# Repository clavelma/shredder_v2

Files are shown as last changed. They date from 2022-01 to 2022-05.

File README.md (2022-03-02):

 # Introduction
 
 #### 1. Motivation
   * The team has chosen to to work on recycling plastic waste during a school project. All the teams members are enthousiast by the idea.

 #### 2. Goal
   * Provide a thecnical and organisational solution tho recycle plastic waste. For this project the plastic essentially comes from 3D printing part.
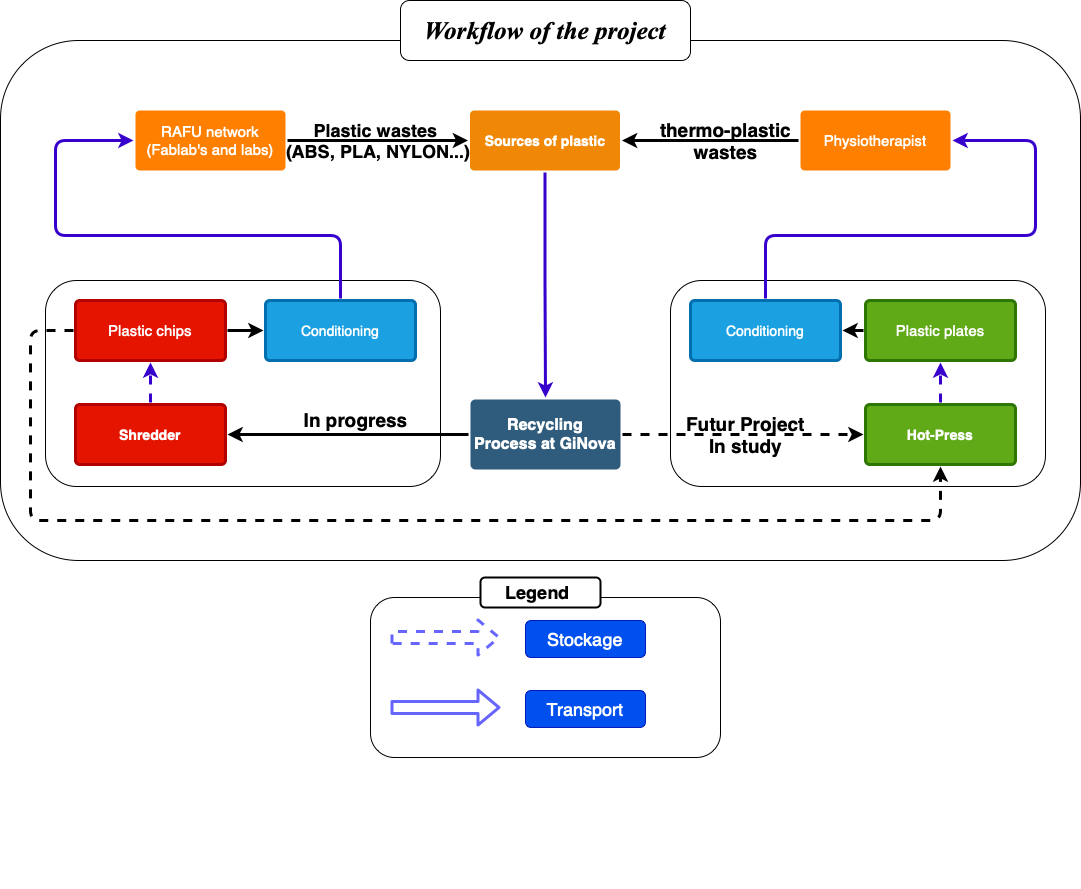
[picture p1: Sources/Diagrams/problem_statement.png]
Problem_statement


 #### 3. History
   * Initiators of the original project: Guillaume Marin
   * URL of other related project: [Precious plasitc](https://preciousplastic.com)
 #### 4. Documentation structure
   * Section 1: Introduction
   * Section 2: Specification
   * Section 3: Design
   * Section 4: Manufacturing
   * Section 5: Assembly
   * Section 6: Use
   * Section 7: Maintenance
   * Section 8: Disposal
 #### 5. Required skills
   * The project echopen need basic knowledge about electrical connection, ...
 #### 6. Contribution process
   * ...
 #### 7. Last update
   * 09/12/2021, 14h, addition of information, Margaux
 #### 8. Project team
   * BIANCIOTTO Tom {tom.bianciotto@grenoble-inp.org}
       * Role in the project: Project manager
       * https://www.linkedin.com/in/tom-bianciotto-b9ba4b1b8
   * CLAVEL Maxime {maxime.clavel@grenoble-inp.org}
       * Role in the project: Data manager
       * https://www.linkedin.com/in/maxime-clavel-36a43a218
   * GASTON Louis {louis.gaston@grenoble-inp.org}
   * LEGARDEUR William {william.legardeur@grenoble-inp.org}
   * LENNE Margaux {margaux.lenne@grenoble-inp.org}
       * Role in the project: Organisation, gantt chart manager
       * https://www.linkedin.com/in/margaux-lenne-27981b208/
   * WILLIE Nsongurua Innocent {nsongurua-innocent.willie@grenoble-inp.org}
       * https://www.linkedin.com/in/nsongurua-willie-3b72781b5
       * Role in the project: Organisation, Advancement manager
#### 9. Licence
   * GPLv3
#### 10. Sponsors and partners
   * Name: Grenoble INP Génie Industriel
      * URL: https://genie-industriel.grenoble-inp.fr/
      * Address: 46 avenue Félix Viallet F-38031 Grenoble cedex 01
   
   * Name: FabMSTIC
      * URL: https://fabmstic.imag.fr/
      * E-mail address: fabmstic@univ-grenoble-alpes.fr
      * Address: 740 rue de la Piscine, 38400 Saint-Martin-d’Hères

   * Name: La Casemate
      * URL: https://lacasemate.fr/
      * E-mail address: accueil@lacasemate.fr
      * Address: 2 place Saint-Laurent 38000 Grenoble

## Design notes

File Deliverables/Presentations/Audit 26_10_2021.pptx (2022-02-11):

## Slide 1

OPEN SOURCE PLASTIC

RECYCLING MACHINE

Mardi 26 Octobre

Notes: WILLIAM

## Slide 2

Table of contents

1 - Recap of the previous audit

2 - Updated Gantt

3 - The installation of the hopper

4 - Wiring diagram

5 - First version of safety rules and regulations

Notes: WILLIAM

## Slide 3

Recap of the previous audit

Germain LEMASSON, FabManager FabMSTIC ; He wants ABS & PLA big ships plastic thanks to our low cost shredder

Manuel FRANÇOIS, Physiotherapist, Orthotist ; He wants new plastic plate thanks to our ‘hoven’ and the unusable piece of plastic given by him

Gantt & risk analysis

Presentation of the client and his expectations

Presentation of the physiotherapist and his expectations

Organisation

Systems engineering of the shredder

CAD and first progress

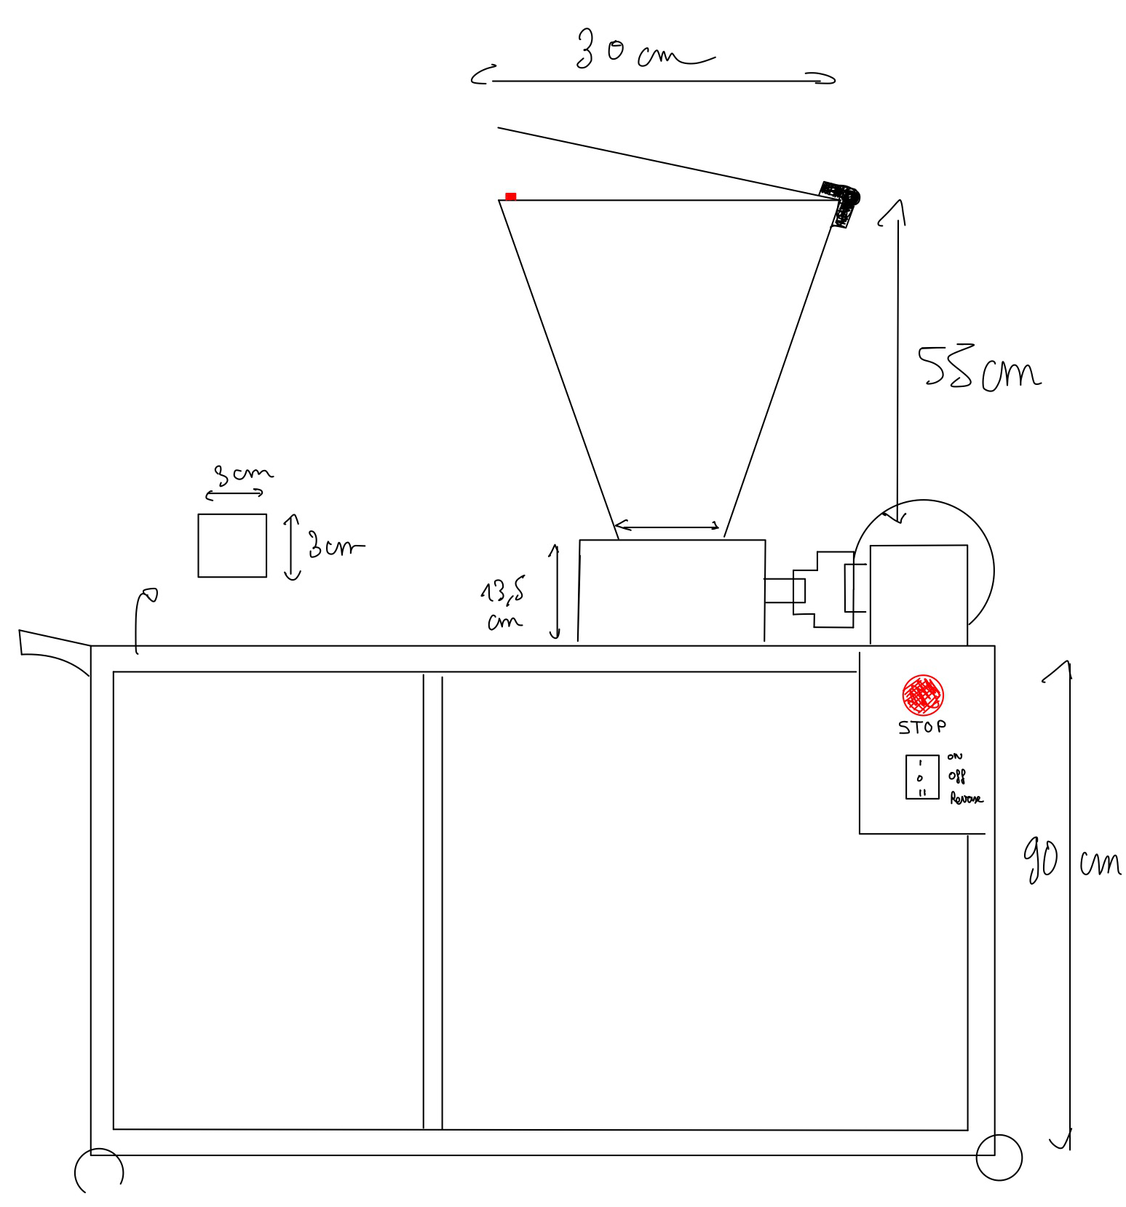
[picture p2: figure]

Stakeholders diagram

CAD of the hopper
Installation of the converter

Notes: MAXIME

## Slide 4

Table of contents

1 - Recap of the previous audit

2 - Updated Gantt

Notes: WILLIAM

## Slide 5

Updated Gantt

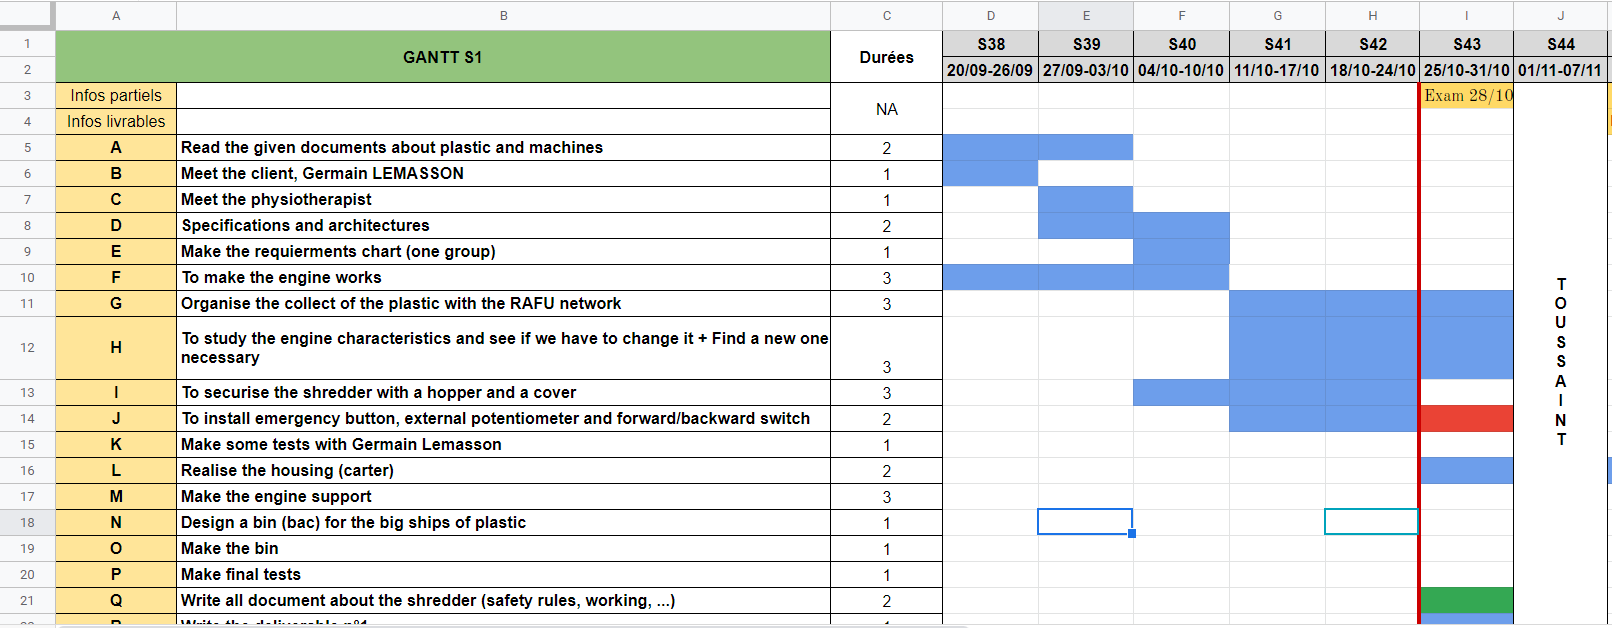
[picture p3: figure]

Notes: Someone else

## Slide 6

Table of contents

1 - Recap of the previous audit

2 - Updated Gantt

3 - The installation of the hopper

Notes: WILLIAM

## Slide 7

The installation of the hopper

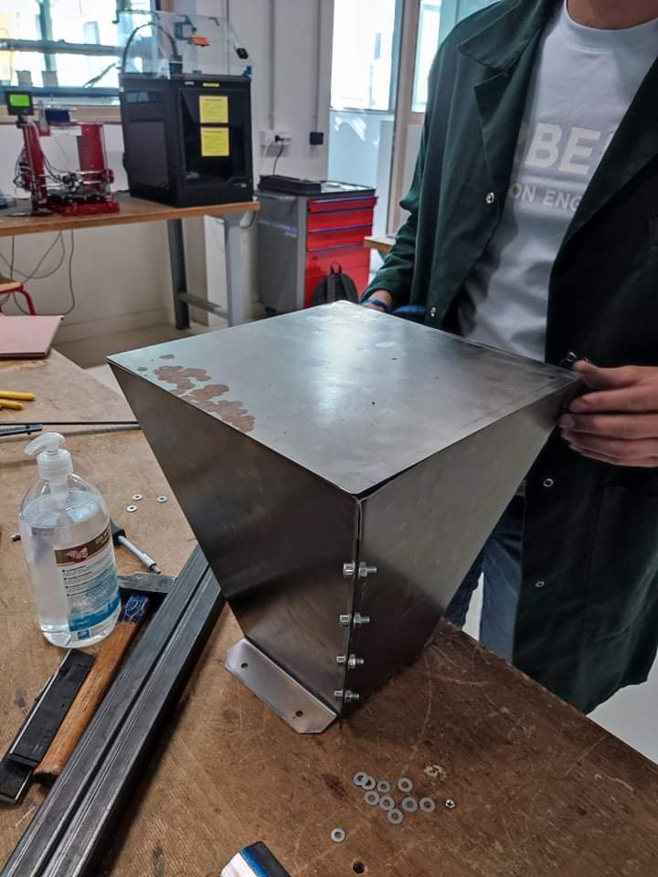
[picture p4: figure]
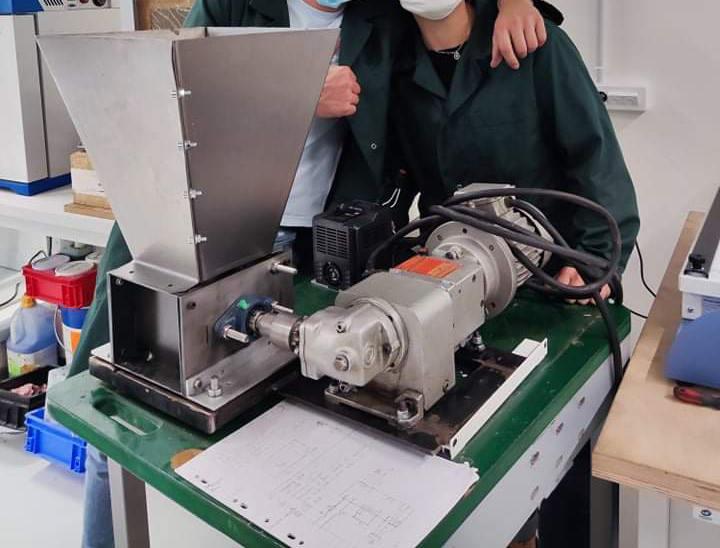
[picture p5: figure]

The final result

1. Bending of the 2 sheets
2. Assembly of the 2 parts
3. Attaching the hopper to the shredder

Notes: MAXIME

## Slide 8

Table of contents

1 - Recap of the previous audit

2 - Updated Gantt

3 - The installation of the hopper

4 - Wiring diagram

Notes: WILLIAM

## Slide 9

Wiring diagram

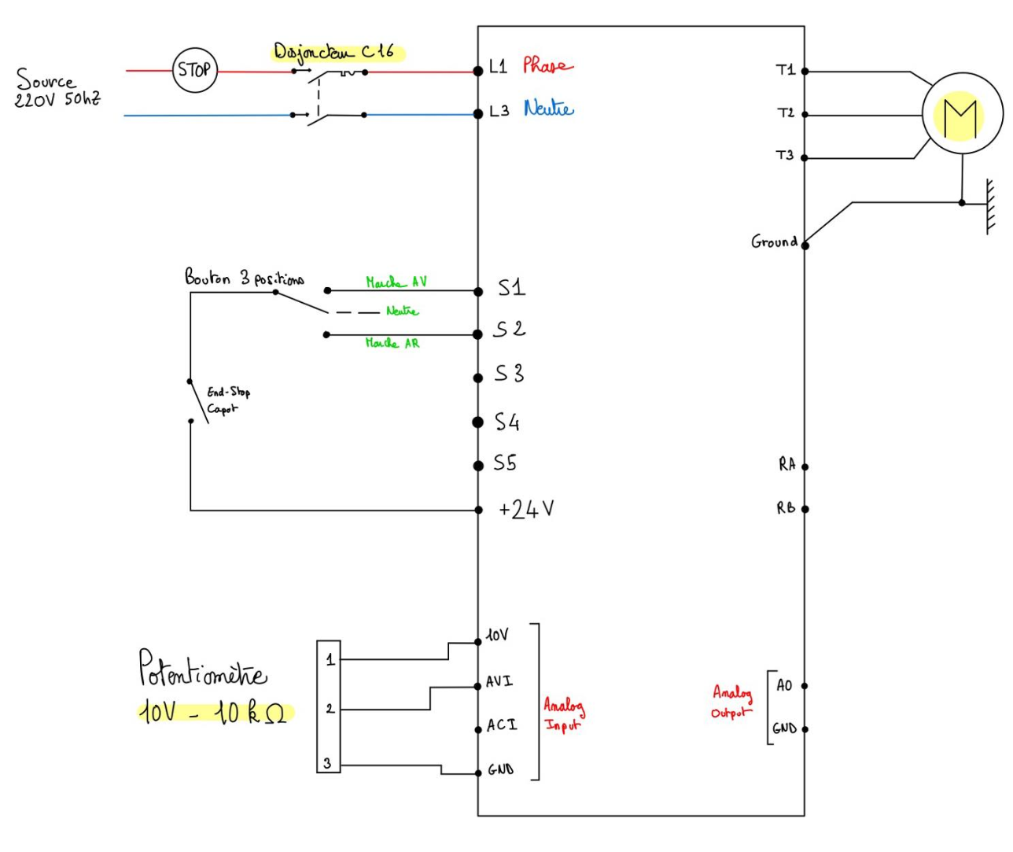
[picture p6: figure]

Buttons that will be present :
- Emergency stop with a circuit breaker (disjoncteur)
- Button on/off
- Button 3 positions
Other elements :
- End stop for the hopper
- A potentiometer
And the engine of course

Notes: Rajouter voyants pour allumer/éteint
Rajouter yellow flashing LED

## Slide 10

Table of contents

1 - Recap of the previous audit

2 - Updated Gantt

3 - The installation of the hopper

4 - Wiring diagram

5 - First version of safety rules and regulations

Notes: WILLIAM

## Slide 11

First version of safety rules and regulations

1. Avoid putting too much plastic into the shredder as this can wear down the motor.
2. When the machine is in motion, putting your hand into the crusher is forbidden to avoid injury.
3. Avoid putting hard objects to avoid damaging the blades.
4. Regularly lubricate and maintain the running parts.
5. Always clean the shredder after using it to shred a particular type of plastic.
6. Keep Jewelries, long hair, or loose clothing (i.e neckties) away from the plastic shredder opening.
7. Always turn off and unplug the power source when the machine is not in use.

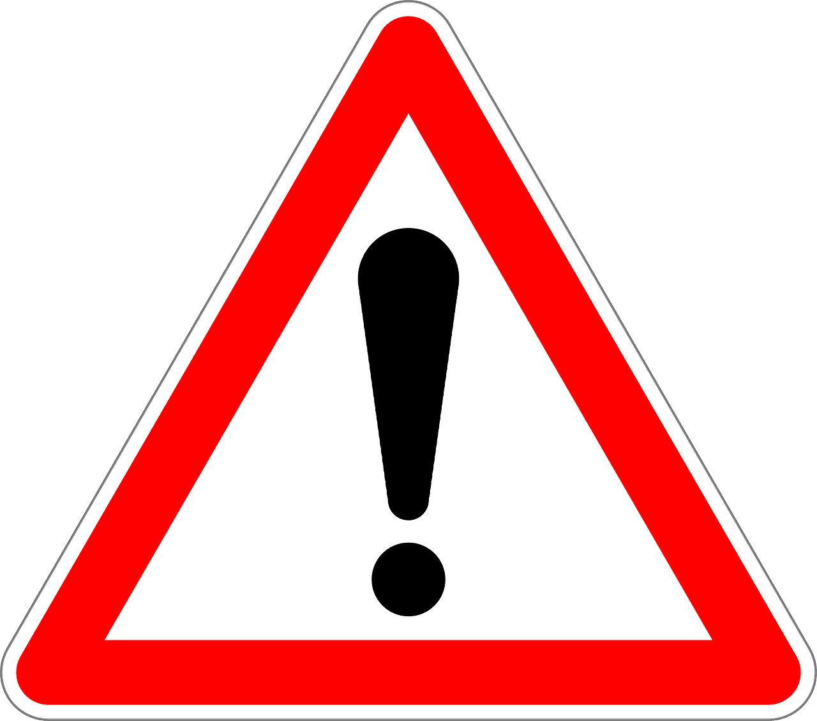
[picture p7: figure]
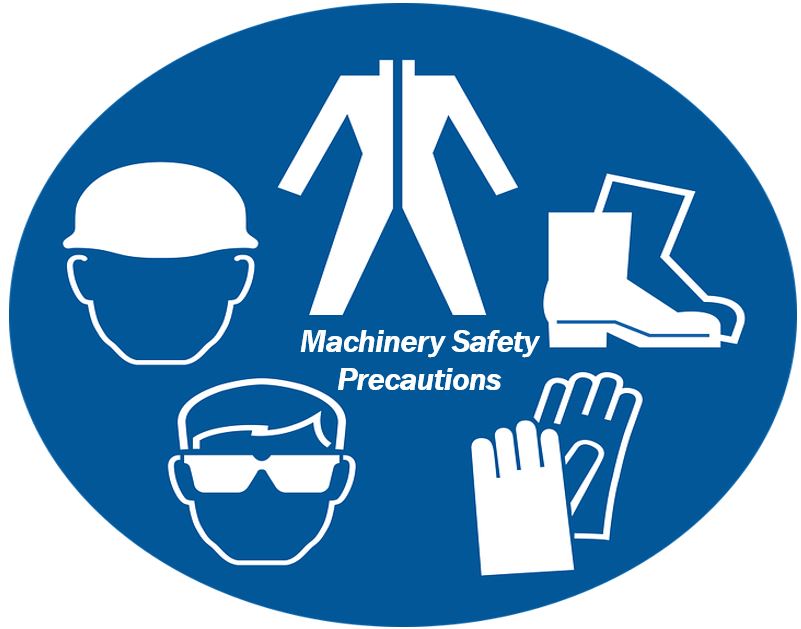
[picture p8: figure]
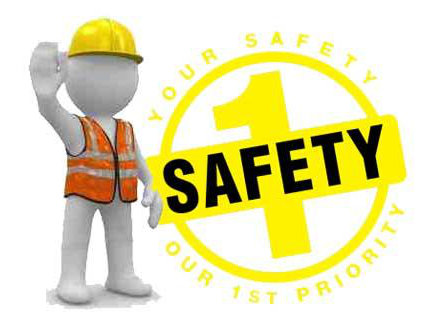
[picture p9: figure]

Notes: Someone else

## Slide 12

Interrogations

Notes: Someone else

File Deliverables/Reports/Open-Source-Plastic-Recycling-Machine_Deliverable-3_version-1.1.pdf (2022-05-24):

# Deliverable 3

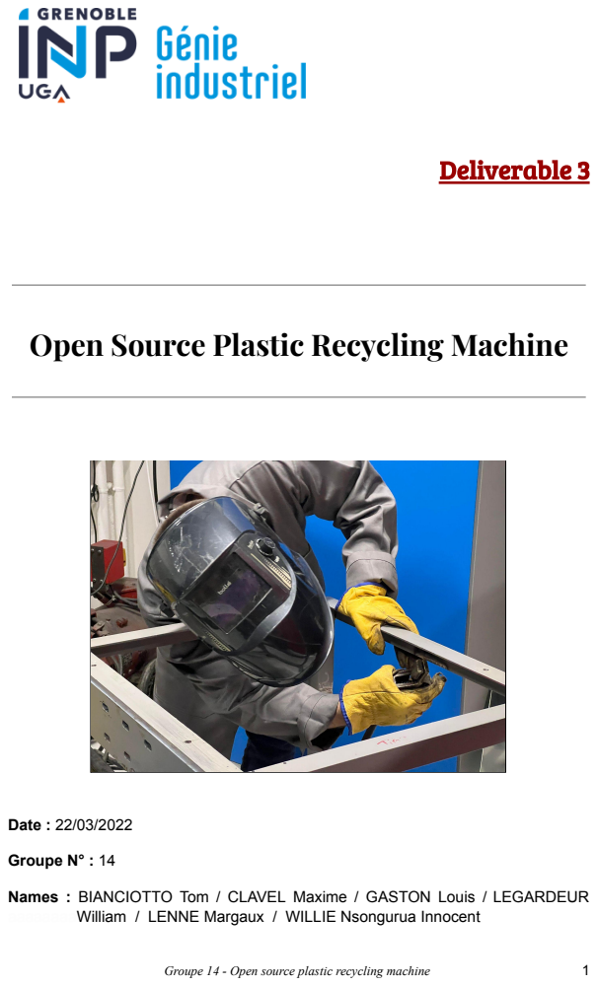
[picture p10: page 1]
Date : 22/03/2022; Groupe N° : 14; Names : BIANCIOTTO Tom / CLAVEL Maxime / GASTON Louis /; LEGARDEUR; Groupe 14 - Open source plastic recycling machine

Open Source Plastic Recycling Machine

aaaaaaaaWilliam / LENNE Margaux / WILLIE Nsongurua Innocent

# SUMMARY

A/ Context of the study - Main objective of the project | 3
B/ Architecture | 4
C/ Verify plan | 5
D/ Simulation (new) | 7
E/ Prototype | 9
F/ Project tasks advancement and achieved work plan | 12
G/ Risk analysis | 13
H/ Work Plan - objective, Key elements, difficulties | 14
APPENDIX 1: GANTT chart | 15
APPENDIX 2: Risk analysis | 17
APPENDIX 3: Cost table | 18
Groupe 14 - Open source plastic recycling machine | 2

## A/ Context of the study - Main objective of the project

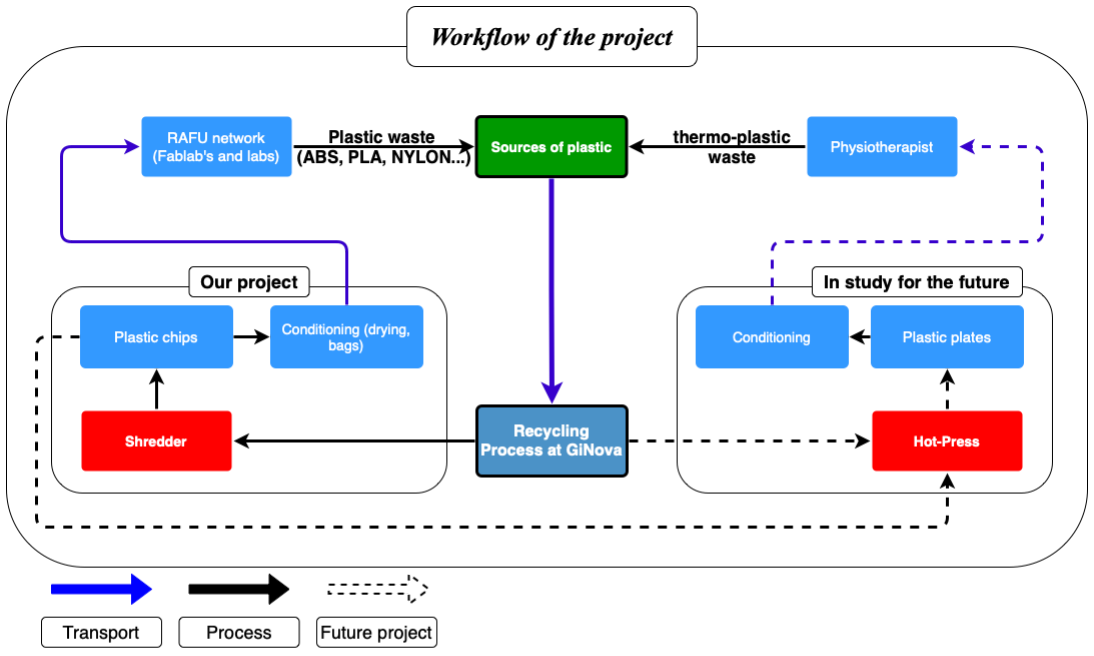
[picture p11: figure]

Figure 1 : Context of the project

The objective of our project can be summarized by finding an open source solution to recycle different kinds of plastic waste. In our more specific situation the objective is to first provide a plastic recycling solution to the RAFU network. This network gathers the labs and Fablab of the UGA. The research and the craft made there, create plastic waste especially with the 3D printing process. It would be a huge improvement if it became possible to recycle these plastics. In the future this solution could be extended to other kinds of actors who use plastics such as physiotherapists who make splints with thermoplastic or industrial materials (such as Chabloz company with nylon waste).

The objective of the group was to find a way to make the creation of 3D printing filament easier with the professional recycling machine available in the fabMSTIC. The main point of improvement is to work on the size of the pieces of plastic that had to be recycled. Another important phase is to organize the collection and the travel between the different recycling spots and users. Another point that could be developed is the creation of plastic plates to give a new life to the plastic collected.

To work on this project, the group was given a prototype of a plastic shredder and a hot-press. These two prototypes were not fully finished and need to be improved in a matter of capacity and mostly about safety to be used properly.

Since the first deliverable the work was focused between a fine study of the way to recycle plastic, the design of the prototypes improvement, and the creation of the Open source documentation on a Github repository. (https://github.com/clavelma/shredder_v2)

Groupe 14 - Open source plastic recycling machine | 3

## B/ Architecture

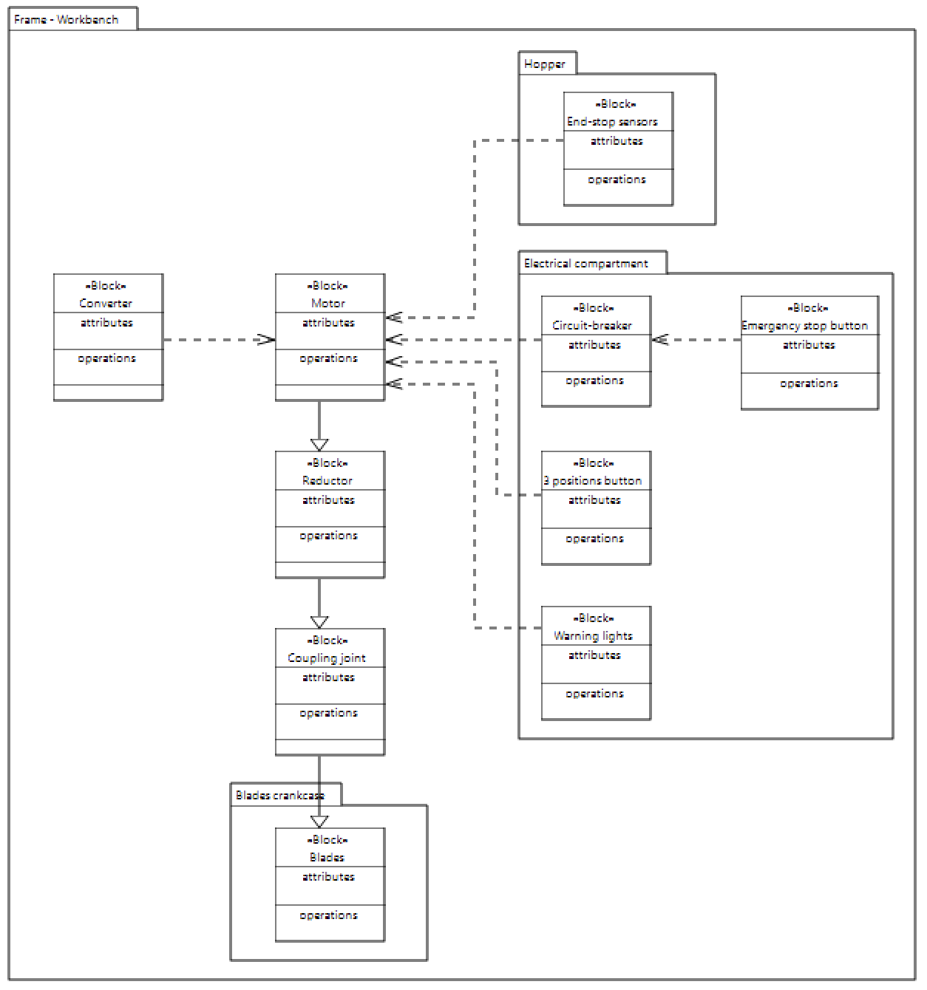
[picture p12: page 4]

To have a better view of the products of our project, we made an Internal block diagram for both the shredder and the compactor. It allows to represent the connections between components but also, and especially, the exchanges of matter, energy and information with the notion of ports.

Groupe 14 - Open source plastic recycling machine | 4

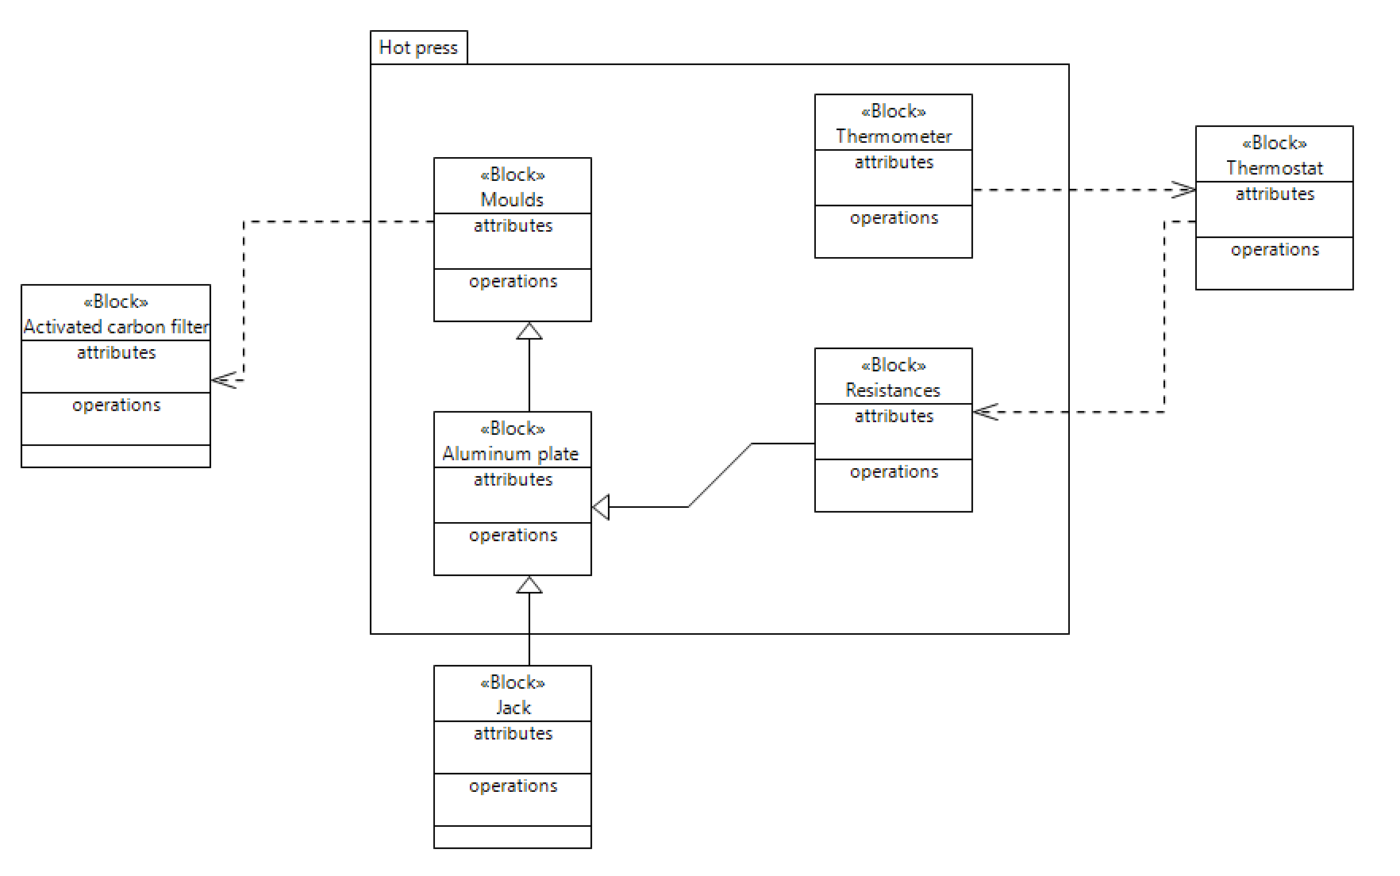
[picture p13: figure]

Figure 2 : Internal block diagram Shredder & Compactor

Informations/ Electrical energy

Forces/ Mechanical energy

Groupe 14 - Open source plastic recycling machine | 5

## C/ Verify plan

In order to follow the requirements requested by the customer, we list them in a table [figure 3] and for each of them we assign one of three levels:

- Not verified: meaning that we have not yet been able to verify this requirement. However, verification plans exist and will be implemented as soon as possible.
- In progress: meaning that we are currently working on the mill to validate this requirement.
- Verified: everything has already been implemented to validate the requirement.
ID requirement | Name | Level of verification
FR1 | The shredder needs to work on a standard 220V 50Hz EU plug. | Verified: use of a converter
FR2 | The shredder needs to respect the 1m50x1mx1m50 maximum volume to avoid cluttering the space. | Verified
FR3 | The shredder needs to shred plastic into chips with a surface inferior to 15 mm² with a tolerance of 5%. | Not verified: requires a test phase when the shredder will be operational
FR4 | The shredder needs to stop in case of emergency in less than 3 seconds. | Not verified: requires a test phase when the shredder will be operational
FR5 | The shredder must be secured to prevent injury on contact (against moving parts and projectiles). | In progress: a hopper and a cover have been installed. Lack a protective cover for rotating parts and the installation of an end-stop button to switch off the engine if the cover is opened
FR6 | The shredder needs to have a power-on and/or operation indication that the operator can see | In progress: provided on the electrical diagram but not connected yet
FR7 | The shredder must not exceed the maximum accepted noise level. | Not verified: requires a test phase when the shredder will be operational
FR8 | The shredder should not transform one of the labs and fablabs of the RAFU network into a storage place for all the plastic chips. | Verified: use of kanban labels to track each bag of chips
FR9 | The shredder needs to have a reverse function in case of blocking or any other mechanical problem. | Verified: thanks to the converter
FR10 | The shredder and its installation should be stable and strong. | Verified: through structural calculations

Figure 3 : Monitoring of the requirements

So we have three requirements that are not yet verified at the time of writing this deliverable. Let us detail the verification plans for these:

- FR3 "The shredder needs to shred plastic into chips with a surface inferior to 15 mm² with a tolerance of 5%." :
Groupe 14 - Open source plastic recycling machine | 6

For the test phase, we will cut different types of grids with different holes in steel using the water jet cutter [see figure 4] (plexiglass is impossible to use because it is brittle and the grate is right under the teeth of the rotating grinder. This grid will be placed under the shredder, just below its blades. Thus, if the chips are too large, they are recovered by the blades and returned to be crushed until they reach the size desired by the customer.

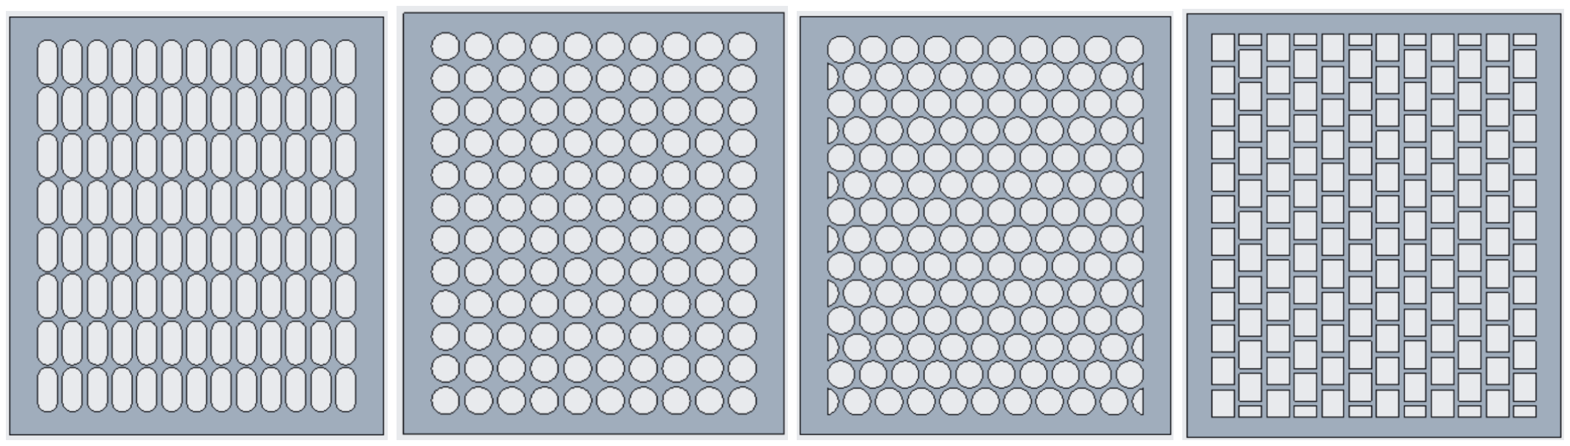
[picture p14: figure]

Figure 4 : Different kind of grid to test

- FR4 "The shredder needs to stop in case of emergency in less than 3 seconds". :

In order to verify this requirement, we plan to use the blocked week to have two people from the group work on the converter ramp study. Indeed, by choosing the right parameters on the one we already have we will be able to configure the new ordered converter correctly once we receive it.

- FR7 "The shredder must not exceed the maximum accepted noise level. :

This requirement will be verified once the prototype is completed. Potential noise sources are mainly from :
→ From the engine
→ From the shredding of the plastic, but the first shredding test we did with the old engine showed us that the noise emitted was still acceptable.
→ From the workbench
Groupe 14 - Open source plastic recycling machine | 7

## D/ Simulation (new)

In the previous deliverables, we were talking about reinforcing the support structure of our workbench, supporting the shredder assembly and the motor, actually made of a 30 mm MDF wooden plate. This idea was quite rushed and our professors asked us to prove the necessity of changing this plate, so now we do :

The system we have, transmits high torque by the upper plate of the table, the reason why is that the motor and the shredder are two independant parts so they must necessarily be attached to a common support : the wooden plate. We would not want it to break under the effect of the engine torque so we decided to make a small simulation of the situation, described on [figure 5] below :

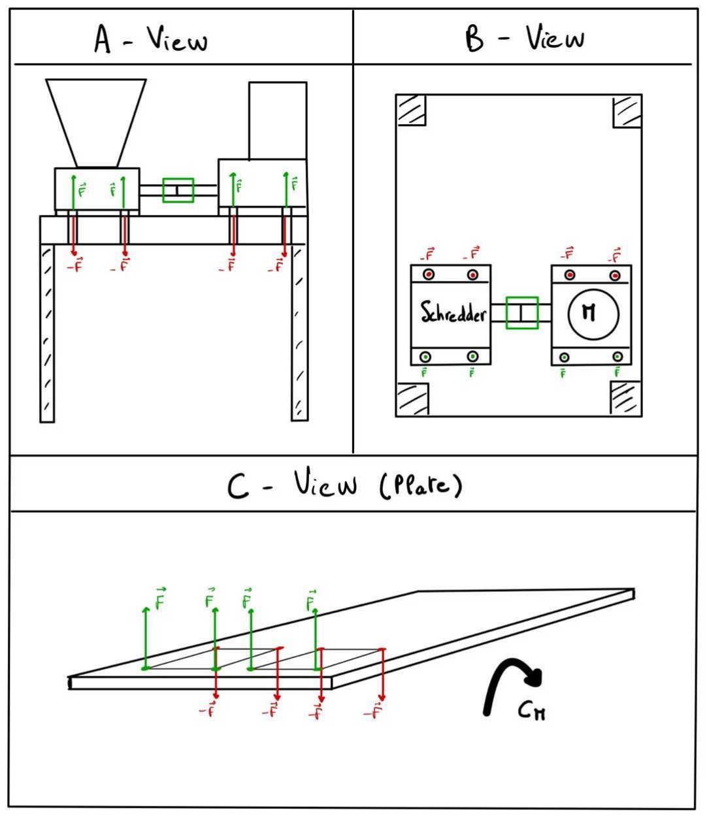
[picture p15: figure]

Figure 5 : Representation of the efforts due to engine torque

Groupe 14 - Open source plastic recycling machine | 8

Now we have a simple but realistic schematic of what will really happen on the plate. We can get further into it by modeling this schematic on a structural calculation software, here we will use ANSYS Workbench.

By assumption, we are considering that the torque is equally distributed in the 8 fixation points, we also make the hypothesis that the radius of the blades is about 8 cm. If we take a torque of 300 N.m (maximum transmitted torque), we obtain (300/0,08)/8 = 470 N on each hole of fixation.

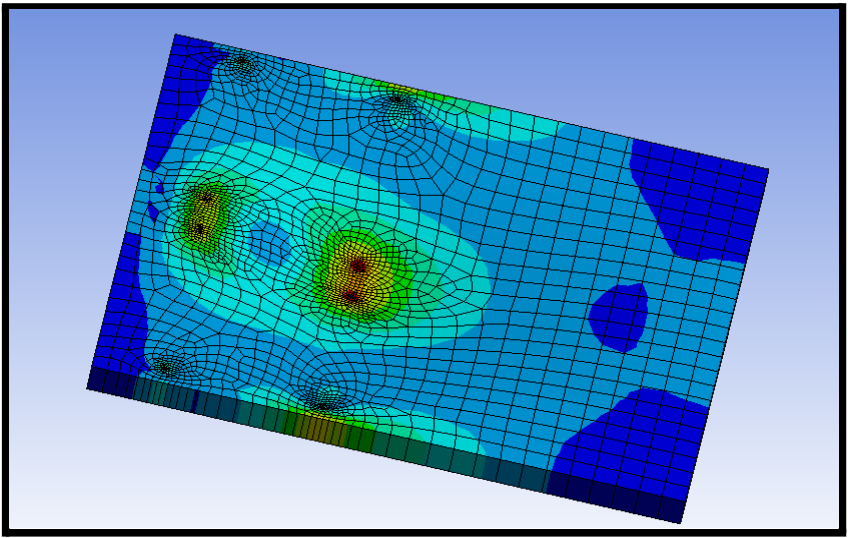
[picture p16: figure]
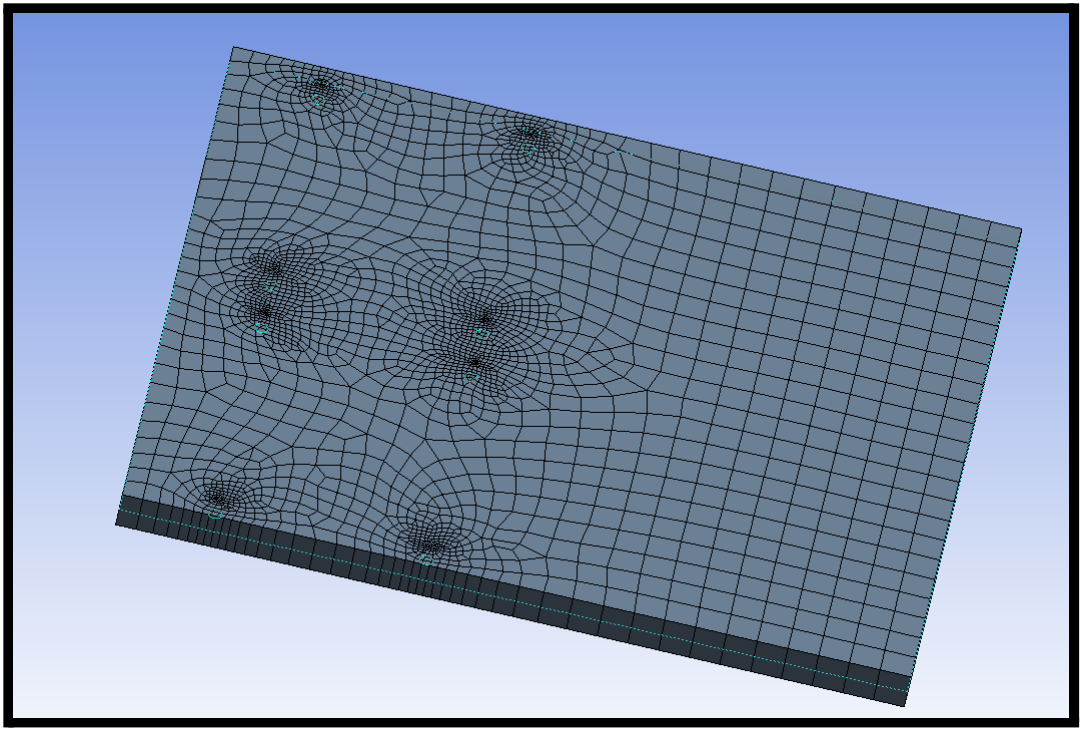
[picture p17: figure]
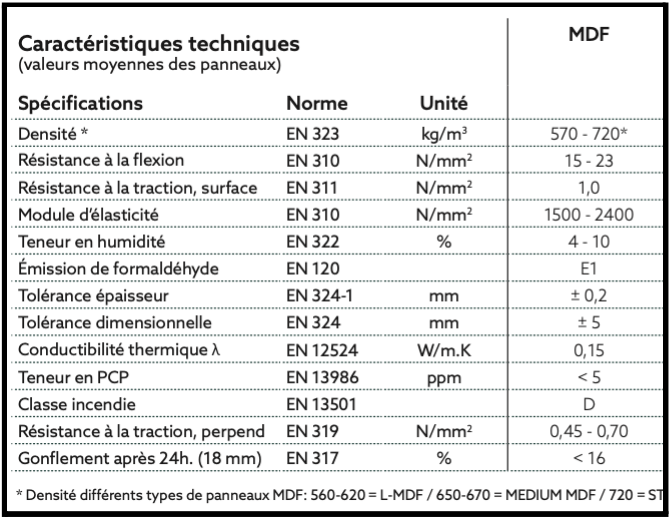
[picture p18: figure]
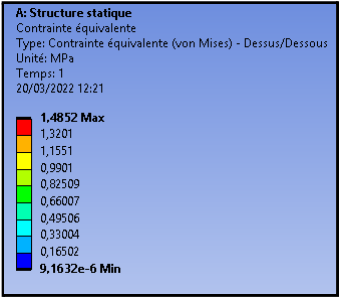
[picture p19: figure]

Figure 6 : Resistance of MDF wood [decopan.com]

As we can see, the maximum constraint is about 1.5 Mpa on the wooden plate, regarding [Figure 6], MDF can absorb around 20 Mpa of bending so the plate seems solid enough to support all these efforts.

Groupe 14 - Open source plastic recycling machine | 9

## E/ Prototype

While waiting for our new adapted gear motor we tried to make as much progress as possible on the structure of our shredder, two important things were missing:

- A chip collection tray
- An electrical compartment

To put these elements in place, it was necessary to add a floor to our frame, so we prepared the structure and welded square steel profiles of 30x30 mm.

We then fixed a wooden plate for the shelf and a plexiglass plate as a front for the different switches: emergency stop, forward/backward/off switch, potentiometer, circuit breaker. A separating sheet has also been installed to prevent people from electrical injuries putting their hands in the electrical part. For safety reasons, all the metal elements will be connected to the ground.

We obtain the following structure (still incomplete) [Figure 7]:

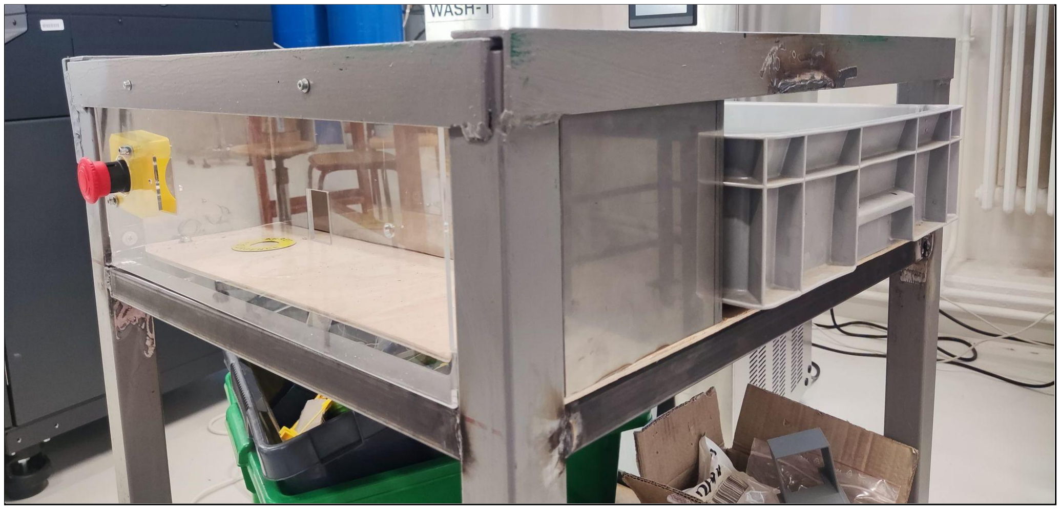
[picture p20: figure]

Figure 7 : Structure of the shredder

Groupe 14 - Open source plastic recycling machine | 10

We also installed our hinges and the opening sensor on the hopper [Figure 8]:

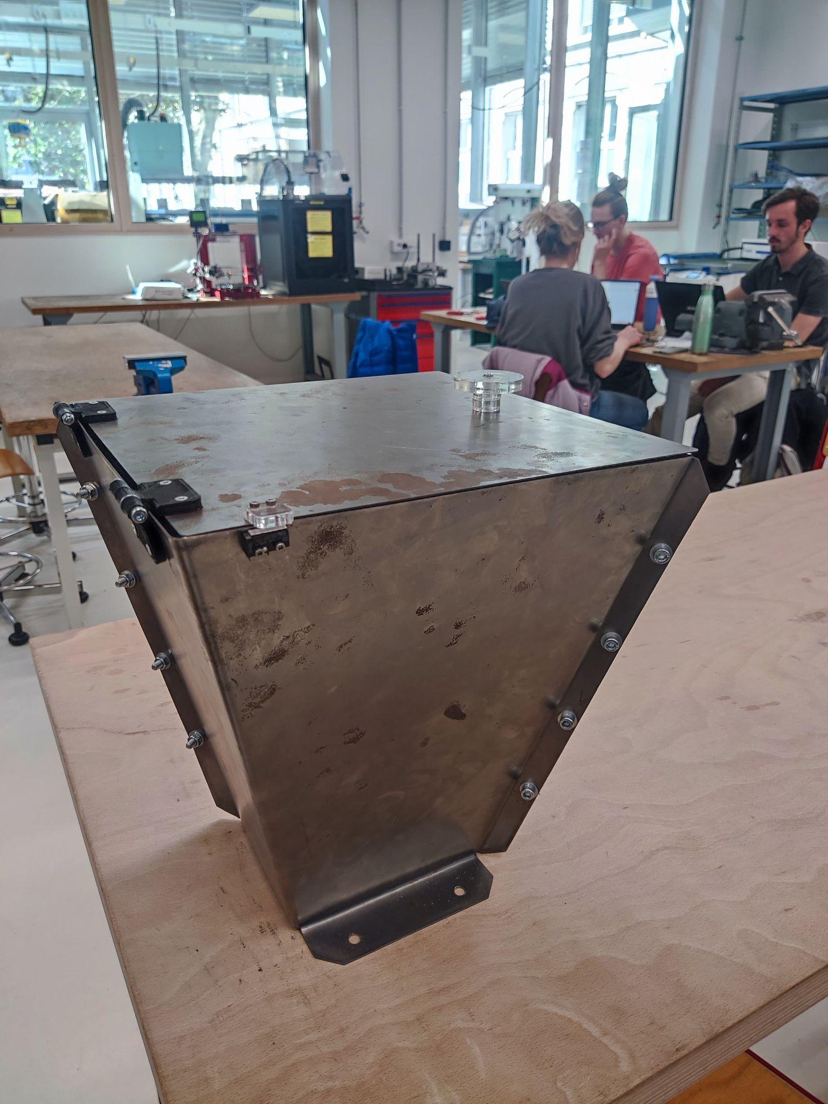
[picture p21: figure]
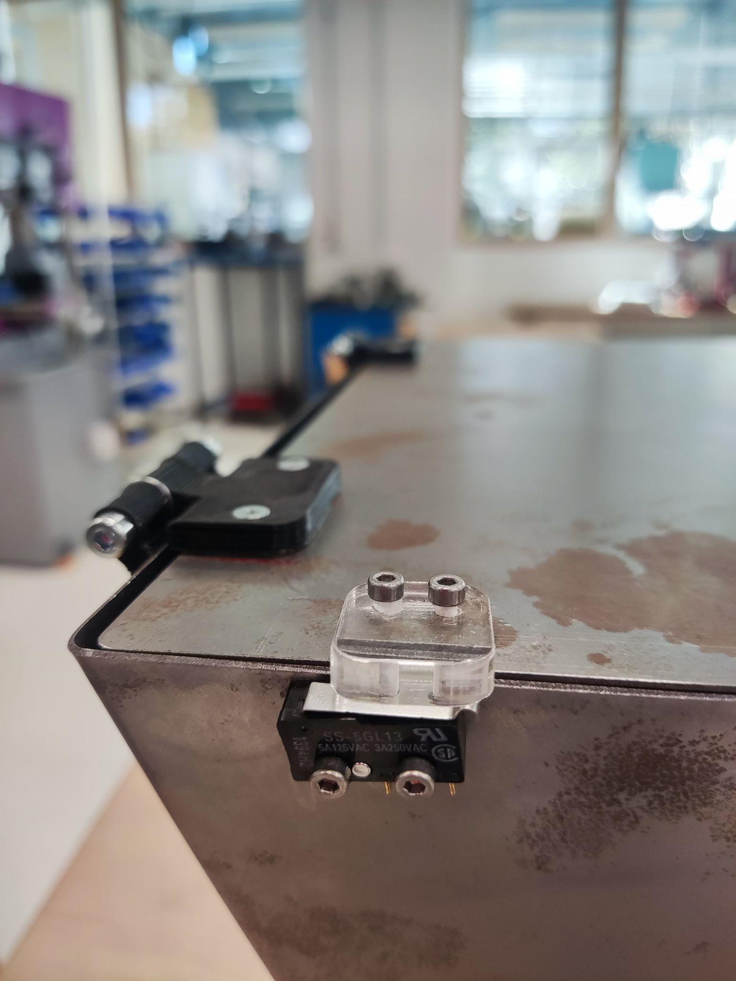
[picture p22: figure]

Figure 8 : Hinges, handle and opening sensor on the hopper of the shredder

We now have to make the various attachments for the transmission according to the specifications of the new gear motor ordered, cut a steel sheet for the shelf (currently made of a poor wooden plate) and an aluminum sheet for an enhanced rigidity of the front panel (currently made of plexiglas).

As explained above (Part C/ Verify plan), we also need to cut out different backflow grids for the chips to determine their optimal size. We therefore go to ENSE3 to make all our cut-outs [Figure 9] :

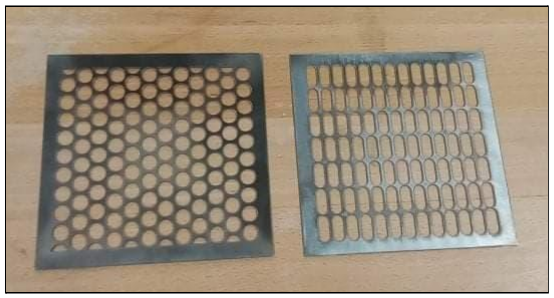
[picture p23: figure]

Figure 9 : Backflow grids for the shredder

Now, the next step for these grids will be to create a sheet metal forming die to form the sheet into a cylinder.

Groupe 14 - Open source plastic recycling machine | 11

## F/ Project tasks advancement and achieved work plan

Since the last audit, the tasks have gone according to the Gantt chart. We only had a one week delay on task D "Systems Engineering" because we had not finished the SysML part of the hot press on papyrus. However, this delay does not have a big impact on our project as it is not on the critical path.

For the next few weeks, we have to pay close attention to task I "Improvement of the shredder" which is a critical path task. Indeed, as planned, this task must be finished by week 15 (11 April - 17 April) in order to make room for the last task of the critical path: "Tests" [see annex 1]. However, if we look at the subtasks of I, we notice that many of them are on stand-by [see figure 10]. The reason for this is that the motor given by Guillaume MARIN (the engineer who gave us a first prototype of the shredder at the beginning of the year) had insufficient torque, as did the second motor we found in Ginova. This necessitated a calculation phase in order to find the torque we needed for shredding plastic. We are now waiting for this new motor and a new converter, as the old one is not suitable for the future motor. [See G/ Risk analysis for more details].

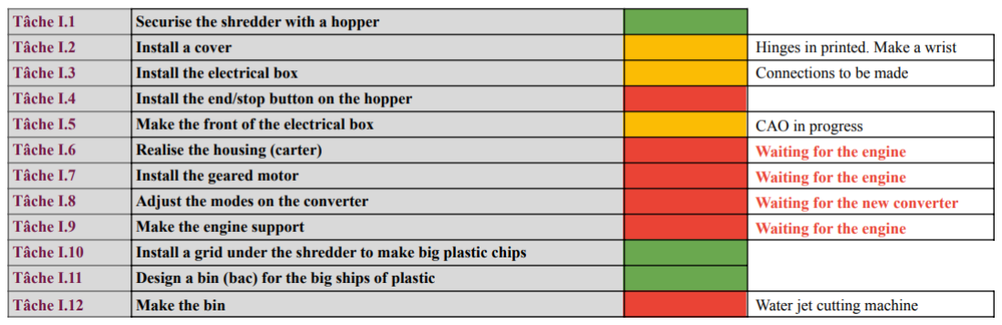
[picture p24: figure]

Figure 10 : Details of task I - Improvement of the shredder
(red = task not started, orange = task in progress, green = task finished)

While waiting for this new engine, we will take advantage of the week blocked for the project activities to make as much progress as possible on the prototype of the shredder. When we receive the motor, all we have to do is install it and connect it to the shredder shaft.

We also made an update of the project cost estimations [appendix 3] where we mainly add the engineering price and the new gearmotor quote with its new converter.

Groupe 14 - Open source plastic recycling machine | 12

## G/ Risk analysis

At the period of the last deliverable, the group got some issue with the engine which was not powerful enough for the shredding task. This possibility was considered in the Risk analysis but the criticality was clearly under-estimated. To not make the same error the group had decided to reconsider all the severity and occurrence levels of the previous Risk Analysis document to create a new revision of the document. This revision number 2 is focused on two main points. First reconsider all the critical levels as said before with the experience we had gained during the first phases of the project in order to highlight all the major risks for the end of the project. The second part of the work in the Risk Analysis is to think about the new issues that could occur in the prototyping and testing phase.

For the new evaluation of the risk levels, we can take the example of the risk of an engine that is too weak to shred that passed from a Criticality 1 to 4 that is clearly more reasonable after experiencing this problem. Some other risks were re-evaluated : to finish the prototyping, we need to receive a new engine with enough torque, a problem in the order could compromise the end of the project. We can also talk about the fact that the lab might be occupied by other students, that could prevent us from working on the prototype. At this period this risk is more important because first year students have some project that needs the lab. The access to the tools and equipment could be pretty difficult during these phases.

Figure 11 : Motor risk in REV1

Figure 12 : Motor risk in REV2

About the New risks that were added they are mainly related to the prototyping and testing phase. A very obvious risk in this kind of phase could be to break a component while mounting it or while testing it. To find a solution to this problem or to try to limit at maximum the chance of this happening, the group had made a list of all the components of the prototype. In this list the group will define what components are the more fragile or the most difficult to replace. This could help to be more careful when we manipulate the more critical parts of the prototype. Another risk could be about the shredding module which could possibly not work as expected. We never saw it work because of the engine issue and we completely do not know how it will shred the plastic parts.

Figure 13 : Risks added in REV2

Groupe 14 - Open source plastic recycling machine | 13

## H/ Work Plan - objective, Key elements, difficulties

As compared to the first few months when we started, we can boldly say that we have a clear work plan and end goal now. In the first few months of our project, we were solely focused on the global perspective of our project, instead of being specific on a particular area (functional shredder). We had indeed underestimated the demand of the work. Thanks to several educating sessions with the professors, we are more focused on the specifics and now have a clear goal.

The objective of our work, in correlation to the topic, is to deliver a functional plastic shredding machine, with detailed documentation on GitHub, as it is an open source project. With this objective in mind, our shredder should be able to shred plastics to the desired fineness, for other usage. The key elements of this machine are the motor, blades, torque and the electrical components of the shredder. To determine the performance of our shredder, different tests will be carried out on the shredding machine. For example, the ratio of the output mass to the input mass will be determined and a high percentage indicates a good shredding process.

So far, we have had a fair share of difficulties in the course of this project, especially as stated above concerning the global and specific objective of our project. We had underestimated the demands of the project and tried to fulfill the global objective in such a short time, which is clearly impossible. Another major difficulty has been with the motor of the shredder. It had a lower capacity and therefore could not power the machine. We finally made a new order but now there is a delay. Also we did not follow completely accurate procedures, this could have been the cause. In the first two deliverables, we did not include SysML diagrams and we had ignored a lot of engineering aspects in our presentations, especially to aid in communicating effectively our project. All these have been rectified. We are gradually but clearly working on delivering a finished prototype.

As regards the documentation on GitHub, as a team, we have made commendable progress. We have clearly defined the task for everyone, and had to redefine roles, so as to get everyone involved in the project and deliver on time. The report takes this format, a weekly update of tasks carried out by each member of the team and their progress, this is done by the project advancement manager. The gantt manager updates the gantt regularly, each member also has a part to update on the platform. The project manager oversees.

Therefore, at the end of the project, we should be able to deliver a functioning shredder, able to shred plastics to the desired fineness, thanks to the grid. And also make it an open source project, thanks to GitHub.

Groupe 14 - Open source plastic recycling machine | 14

# APPENDIX 1: GANTT chart

Link to go to the drive with the gantt chart (to see the sub-tasks): https://docs.google.com/spreadsheets/d/1zl9KApmCFzgjy7fXfSUUbfGAa_7RfqJYZSNwacTICsc/edit?usp=sharing (https://docs.google.com/spreadsheets/d/1zl9KApmCFzgjy7fXfSUUbfGAa_7RfqJYZSNwacTICsc/edit?usp=sharing)

You can also see directly a sample below :

Groupe 14 - Open source plastic recycling machine | 15

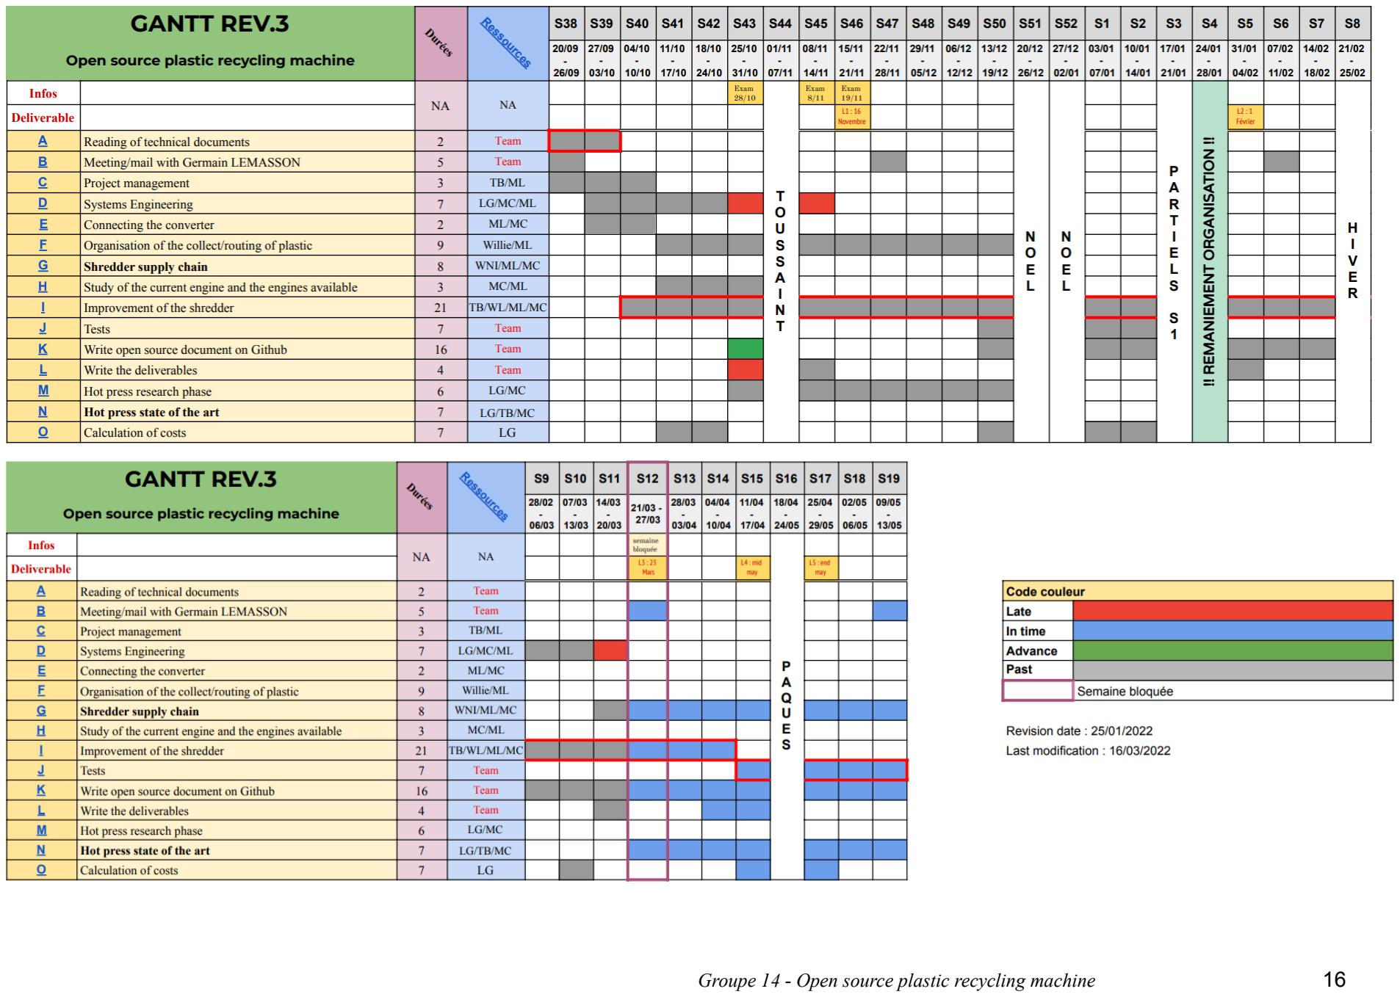
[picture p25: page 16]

Groupe 14 - Open source plastic recycling machine | 16

# APPENDIX 2: Risk analysis


Groupe 14 - Open source plastic recycling machine | 17

# APPENDIX 3: Cost table


Groupe 14 - Open source plastic recycling machine | 18

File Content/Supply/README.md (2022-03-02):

# **Supply**

*Dans notre projet, nous parlerons de supply afin d'assurer le contrôle des différents plastiques passant dans le broyeur. Nous avons alors chercher un moyen de connaître l'origine, le type et la quantité de plastique broyé, l'identité de la personne utilisant le broyeur, ainsi que les différentes opérations subies par le plastique. Afin d'assurer cette traçabilité, nous avons alors pensé à nous inspirer de la méthode kanban que nous avons vu en 1ere année d'école d'ingénieur.   *

## **Storage**

Dans notre logistique, lorsque du plastique sera broyé avec le broyeur, les copeaux tomberont dans un grand bac en plastique. Ensuite les copeaux passeront dans le séchoir (étape non obligatoire mais recommandée surtout si les copeaux sont destinés à recréer du filament pour les imprimantes 3D). Finalement, ils seront placé dans un 

## **Kanban label**

kanban_label

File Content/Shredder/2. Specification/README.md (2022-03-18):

# **Specification**

*The specification consists in describing the product with a "black box" external view to capture the intermediate technical objects (stakeholders, external interfaces, services, and constraints) that serve to, *in fine*, elucidate the product requirements.*

## **How to document the specifications?** 
  
## **1. Stakeholders:**

stakeholders_shredder drawio

## **2. External interfaces**

*The image below shows the external interfaces of  ADD-ONS of XYZ cargo as a graph*

Image of External interfaces of XYZ cargo-ADD ONS

<a href="https://app.diagrams.net/?libs=general#Hamerezoji1362%2Fdrawio-github%2Fmaster%2FExternal%20interfaces.drawio">Edit As New</a> | <a href="https://app.diagrams.net/#Hamerezoji1362%2Fdrawio-github%2Fmaster%2FExternal%20interfaces.png">Edit in diagrams.net</a>
</details>

### Template of external interfaces
   
   * Clients
       * needs
   * Users
       * use
       * repair
   * Partners
       * data
       * technical support
   * Media
       * reproduce
       * data
   * European standards
       * laws
       * norms
       * security
   * Environment
       * supply
       * adapt
       * reuse
       * technical support
  
 Image of stakeholder diagram for template
  
   *The link below can be used to define the external interfaces of your project/product.*
  
  <a href="https://app.diagrams.net/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">Edit As New</a> | <a href="https://app.diagrams.net/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">Edit in diagrams.net</a>

## 3. Service *(synonyms: external function, capability)* 
<details>
  <summary>Click to see the guideline!</summary>
  
- **Definition:** *A service is an effect intended by a stakeholder resulting from the interaction of the product with its environment (i.e. what the  product is for).*

- **Comments:**
  - *Services provide users with an exchange value that can be included in an economic system (e.g. airlines buy flight hours).*
  - *Services are intended effects that can be observed from outside the product ("black box" external view), but not from outside an internal component ("white box" internal view).*
  - *Services are defined in a solution neutral-way.*
  - *Services can be stated as follows: The [Product] shall enable [Stakeholder] [Action verb] (e.g. The product shall enable end-user to clean its teeth)*
  - *we often reason in terms of action verbs to communicate expected behaviors, so it would be nice to be able to search designs with action verbs*
</details>

<details>
  <summary>Click to see the example!</summary>
  
 ```
  What does contain the minimum documentation of the service to stakeholders?
  
  Example of services for ADD-ONS of XYZ Cargo
  
    - The ADD-ONS shall enable the food producer to store food
      - 1.1 solid (10 kilos)
      - 1.2 liquid (5 litrs)
    - The ADD-ONS shall enable the food producer to heat food
      -  2.1solid (150 deg Celcius)
      - 2.2 liquid (80 deg Celcius)
    - The ADD-ONS shall enable the food producer to cool down food for 4 hours
      - 3.1 solid (6 deg Celcius)
      - 3.2 liquid (6 deg Celcius)
      
    - ...
  ```
 </details>

### Template of services
  
   * Services to clients
       * The shredder shall enable the ABS&PLA plastic from 3D printing scraps to be reduce into medium or small chips.
       * The shredder shall enable the thermoformable plastic from thermoformable plastic plate scraps to be reduce into medium or small chips.
   * Services to users
       * The shredder shall enable the plastic from user's personal collection to be reduce into medium or small chips.
   * Services to partners
       * The shredder shall enable the plastic from partner's personal collect to be reduce into medium or small chips.
   * Services to media
       * The shredder will serve as a functional example of low tech solution for plastic recycling.
   * Services to european standards
       * The shredder will meet the safety and working standard conditions based on european standards. 
   * Services to environment
       * The shredder in all ramifications, will be safe to use and environmental friendly.

## 4. Constraint *(Synonyms: non function requirement)*

### Template of constraints
  
   * The shredder should be dismantled for recycling purposes
   * The shredder should be realise and operate in a low tech philosophy
   * The shredder should follow the european standards
   * Open source community should be able to reproduce it
   * User should be able to use it in security
   * Ginova should be able to handle the maintenance
   * The shredder should be incorporating in Ginova
   * The shredder should be able to shred the plastic from the collect
   * The shredder should be built using the maximum of the existing prototype
   * The shredder assembly and user should be accessible and open source
   * The shredder should be realised thanks to the RAFU network facility
   * The shredder should be able to go forward and to go backward

## **5. Requirement**
 
 ### Template of requirements
    
   * FR1:  The shredder needs to work on a standard 220V 50Hz EU plug
   * FR2:  The shredder needs to respect the 1m50x1mx1m50 maximum volume
   * FR3:  The shredder needs to shred plastic into chips with a surface inferior to 1cm²
   * FR4:  The shredder needs to stop in case of emergency in less than 3 seconds
   * FR5:  The shredder must be secured to prevent injury on contact (against moving parts and projectiles)
   * FR6:  The shredder needs to have a power-on and/or operation indication that the operator can see
   * FR7:  The shredder must not exceed the maximum accepted noise level
   * FR8:  The shredder should not transform one of the labs and fablabs of the RAFU network into a storage place for all the plastic chips.
   * FR9:  The shredder needs to have a reverse function in case of blocking or any other mechanical problem
   * FR10: The shredder and its installation should be stable and strong.

(The effects of vibration can be severe. Unchecked vibration can accelerate rates of wear (e.g., reduce bearing life) and damage equipment. Vibrating machinery can create noise, cause safety problems and lead to degradation in plant working conditions.)

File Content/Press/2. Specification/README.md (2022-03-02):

# **Specification**

*The specification consists in describing the product with a "black box" external view to capture the intermediate technical objects (stakeholders, external interfaces, services, and constraints) that serve to, *in fine*, elucidate the product requirements.*

## **How to document the specifications?** 
  
## **1. Stakeholders:**

stakeholders_shredder drawio

## **2. External interfaces**

*The image below shows the external interfaces of  ADD-ONS of XYZ cargo as a graph*

Image of External interfaces of XYZ cargo-ADD ONS

<a href="https://app.diagrams.net/?libs=general#Hamerezoji1362%2Fdrawio-github%2Fmaster%2FExternal%20interfaces.drawio">Edit As New</a> | <a href="https://app.diagrams.net/#Hamerezoji1362%2Fdrawio-github%2Fmaster%2FExternal%20interfaces.png">Edit in diagrams.net</a>
</details>

### Template of external interfaces
   
   * Clients
       * needs
   * Users
       * use
       * repaire
   * Partners
       * data
       * technical support
   * Media
       * reproduce
       * data
   * European standards
       * laws
       * norms
       * security
   * Environment
       * supply
       * adapt
       * reuse
       * technical support
  
 Image of stakeholder diagram for template
  
   *The link below can be used to define the external interfaces of your project/product.*
  
  <a href="https://app.diagrams.net/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">Edit As New</a> | <a href="https://app.diagrams.net/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">Edit in diagrams.net</a>

## 3. Service *(synonyms: external function, capability)* 
<details>
  <summary>Click to see the guideline!</summary>
  
- **Definition:** *A service is an effect intended by a stakeholder resulting from the interaction of the product with its environment (i.e. what the  product is for).*

- **Comments:**
  - *Services provide users with an exchange value that can be included in an economic system (e.g. airlines buy flight hours).*
  - *Services are intended effects that can be observed from outside the product ("black box" external view), but not from outside an internal component ("white box" internal view).*
  - *Services are defined in a solution neutral-way.*
  - *Services can be stated as follows: The [Product] shall enable [Stakeholder] [Action verb] (e.g. The product shall enable end-user to clean its teeth)*
  - *we often reason in terms of action verbs to communicate expected behaviors, so it would be nice to be able to search designs with action verbs*
</details>

<details>
  <summary>Click to see the example!</summary>
  
 ```
  What does contain the minimum documentation of the service to stakeholders?
  
  Example of services for ADD-ONS of XYZ Cargo
  
    - The ADD-ONS shall enable the food producer to store food
      - 1.1 solid (10 kilos)
      - 1.2 liquid (5 litrs)
    - The ADD-ONS shall enable the food producer to heat food
      -  2.1solid (150 deg Celcius)
      - 2.2 liquid (80 deg Celcius)
    - The ADD-ONS shall enable the food producer to cool down food for 4 hours
      - 3.1 solid (6 deg Celcius)
      - 3.2 liquid (6 deg Celcius)
      
    - ...
  ```
 </details>

### Template of services
  
   * Services to clients
       * The shredder shall enable the ABS&PLA plastic from 3D printing scraps to be reduce into big or medium chips
       * The shredder shall enable the thermoformable plastic from thermoformable plastic plate scraps to be reduce into big or medium chips
   * Services to users
       * The shredder shall enable the plastic from user's personal collect to be reduce into big or medium chips
   * Services to partners
       *  The shredder shall enable the plastic from partner's personal collect to be reduce into big or medium chips
   * Services to media
       * x
   * Services to european standards
       * x 
   * Services to environment
       * x 

## 4. Constraint *(Synonyms: non function requirement)*

### Template of constraints
  
   * The shredder should be dismantled for recycling purposes
   * The shredder should be realise and operate in a low tech philosophy
   * The shredder should follow the european standards
   * Open source community should be able to reproduce it
   * User should be able to use it in security
   * Ginova should be able to handle the maintenance
   * The shredder should be incorporating in Ginova
   * The shredder should be able to shred the plastic from the collect
   * The shredder should be built using the maximum of the existing prototype
   * The shredder assembly and user should be accessible and open source
   * The shredder should be realised thanks to the RAFU network facility
   * The shredder should be able to go forward and to go backward

## **5. Requirement**
 
### Template of requirements
    
   * FR1: The compactor needs to work on a standard 220V 50Hz EU plug
   * FR2: The compactor needs to be able to melt PLA (175°C)
   * FR3: The compactor needs to compact plastic plates with a thickness of 1.6, 2.5 and 3.2 mm
   * FR4: The compactor needs to filter the toxic air
   * FR5: The compactor needs to be isolated
   * FR6: The compactor needs to be safe for the operator (heat)
   * FR7: The compactor needs to have a power-on and/or operation indication that the operator can see
   * FR8: The compactor should have a thermometer (to set the temperature)

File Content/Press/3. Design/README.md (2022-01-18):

# Design

*"To design" refers to the process of originating and developing a plan for a product. So, the product models provide consideration of concepts of product design. Product models serve to answer questions that interest multiple views on the product. Among the product views, there is an agreed-upon ontology of product models named Function-Behaviour-Structure (FBS) where:*

- **Function (F)** stands for **“what the object is for”.**
- **Behaviour (B)** stands for **“what the object does”.**
- **Structure (S)** stands for **“what the object consists of”.**

Image of FBS of design

> *Figure 1. Same function, different behaviour, different structure (Rosenman & Gero, 1998)* 

*Moreover, it should describe the complexity of the product via:* 
- **Modular architecture** that describes **“architecture of functions and instructions of the product”.**

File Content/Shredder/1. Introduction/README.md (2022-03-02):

# Introduction

*The introduction to the documentation aims to provide more details about the project goal, and context. This introduction should allow the reader to first understand the motivation of the project and also who is involved or has been involved in its creation. As this documentation structure aims at fostering the reuse of the technical contents of the project, it is important to understand well the context.*

<details>
  <summary>Click to see the guideline and examples!</summary>
  
## Motivations

*This section addresses the question: Why are you starting this project?*

As an example:
  
The project [BCN3D Moveo](https://github.com/BCN3D/BCN3D-Moveo/) is motivated by the high cost 
of the materials that undergraduate students must use for learning how to engineer mechatronics systems.

## Goals

*This section addresses the question: What will be delivered in this project?* 

As an example: 
  
The project [BCN3D Moveo](https://github.com/BCN3D/BCN3D-Moveo/) is an open source robotic arm 
that everyone should be able to replicate - with or without modification - at home without the need for highly 
technical knowledge and expensive materials. 
The robotic arm will support several of the existing training itineraries: 
mechanical design, automation, industrial programming, etc.

## History

*Here it is of neccessity to acknowledge the existing sources that have been used in this project with locations*

- Initiators of the original project
- URL of the original project
- URL of other related projects 

## Documentation structure

*How is your documentation organized?*

These guidelines will provide you with a standard structure that is mainly following the product 
life cycle and the technological decomposition. It is implemented in the documentation template available in this project. 
  
For example:
- Introduction
- Specification
- Design 
- Manufacturing
- Assembly
- Use
- Maintenance
- Disposal

And inside each of the sections, if required:
- Mechanical
- Electronic 
- Software 

## Required skills

*What is the specific knowledge a maker should own to reuse - with or without modification - your product??*

For example:
  
The project echopen need basic knowledge about the medical ultrasound technology such as ultrasound imaging, 
a matter of acoustical impedance, etc.  

## Contribution Process

*Describe here how a maker can contribute to your project*

-  Example of a contribution process:
  - Post an [issue] and briefly outline the changes you plan to make
  - If you are looking for input on what to contribute, browse the issues with the Requests or Bug label
  - Describe branches
  - Describe what a Pull Request (PR) shall contain (detailed description of changes, a summary of the test, 
    issue numbers that the PR resolves)
  - Specify code style 
  - Contributor license agreement

## Last updates 

*What is the last update of your documentation?*

- Last modification (date, time, object of modification, who,...)

## Project team

*Describe here who is the leader and the main contributors of the project*

- Name {E-mail}
  - domain of expertise and role in the project
  - link to personal web page

## License

*What open-source hardware license your project complies with?*

- [Comparison of free and open-source software licences](https://en.wikipedia.org/wiki/Comparison_of_free_and_open-source_software_licences)
- [license of open hardware projects](https://opensource.com/law/15/2/intro-open-hardware-licensing#:~:text=Open%20source%20hardware%20is%20hardware,on%20their%20hardware%20at%20all.)

## Sponsors and Partners

Who is sponsoring your project?

- URL:
- Name:
- E-mail address:

  </details>
  
### Template of introduction

 #### 1. Motivation
   * The team has chosen to work on recycling plastic waste during a school project. All the teams members are enthusiastic about the idea.

 #### 2. Goal
   * Provide a technical and organisational solution to recycle plastic waste. For this project the plastic essentially comes from 3D printing part.

 #### 3. History
   * Initiators of the original project: Guillaume Marin
   * URL of other related project: [Precious plasitc](https://preciousplastic.com)
 #### 4. Documentation structure
   * Section 1: Introduction
   * Section 2: Specification
   * Section 3: Design
   * Section 4: Manufacturing
   * Section 5: Assembly
   * Section 6: Use
   * Section 7: Maintenance
   * Section 8: Disposal
 #### 5. Required skills
   * The project plastic recycling machine needs basic knowledge about electrical connection, ...
 #### 6. Contribution process
   * ...
 #### 7. Last update
   * 01/3/2022, 14h, Edited, Nsongurua
 #### 8. Project team
   * BIANCIOTTO Tom {tom.bianciotto@grenoble-inp.org}
       * Role in the project: Project manager
       * https://www.linkedin.com/in/tom-bianciotto-b9ba4b1b8
   * CLAVEL Maxime {maxime.clavel@grenoble-inp.org}
       * Role in the project: Electronic and Systems Engineering manager 
       * https://www.linkedin.com/in/maxime-clavel-36a43a218
   * GASTON Louis {louis.gaston@grenoble-inp.org}
       * Role in the project: Data manager
   * LEGARDEUR William {william.legardeur@grenoble-inp.org}
   * LENNE Margaux {margaux.lenne@grenoble-inp.org}
       * Role in the project: Organisation, gantt chart manager
       * https://www.linkedin.com/in/margaux-lenne-27981b208/
   * WILLIE Nsongurua Innocent {nsongurua-innocent.willie@grenoble-inp.org}
       * Role in the project: Progress manager
       * https://www.linkedin.com/in/nsongurua-willie-3b72781b5
#### 9. Licence
   * GPLv3
#### 10. Sponsors and partners
   * Name: Grenoble INP Génie Industriel
      * URL: https://genie-industriel.grenoble-inp.fr/
      * Address: 46 avenue Félix Viallet F-38031 Grenoble cedex 01
   
   * Name: FabMSTIC
      * URL: https://fabmstic.imag.fr/
      * E-mail address: fabmstic@univ-grenoble-alpes.fr
      * Address: 740 rue de la Piscine, 38400 Saint-Martin-d’Hères

   * Name: La Casemate
      * URL: https://lacasemate.fr/
      * E-mail address: accueil@lacasemate.fr
      * Address: 2 place Saint-Laurent 38000 Grenoble

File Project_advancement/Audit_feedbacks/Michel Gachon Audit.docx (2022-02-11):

Requirement = what we propose to the client

make a table cross the line that are good

Important to do the revisions of documents (especially for Risk analysis that evolve a lot)

Manage the discussion with the customer to check regularly his needs.

anticipate meeting with customer

huge impact 3

sure 3

multiply the 2 figures

juste analyse 6,9,4 risk the other can be let down

→ faire évoluer au fil du temps

toujours 2 personnes responsables par livrable pour mettre à jour les documents (analyse des risques, gantt, requirements…)

identify the critical path

be careful with the examheiiiin

do the schedule for the whole year with less details, we can do more detailed schedules for semester for example.

Keep the annex on date for each deliverable to show how the evolution of the project

do the criteria analysis and logical structure.

Put the type of final deliverable (prototype + all the documentation) in the L1

__________________________________________

Audit

refaire toute l’analyse des besoin

faire une architecture logique

faire une IS complète sur la presse et se diviser le travail proprement

make studies

Faire un vrai gantt sur un logiciel spécialisé

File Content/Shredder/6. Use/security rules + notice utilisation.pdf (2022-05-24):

# Utilisation du broyeur de plastique

RISQUES ENCOURUS - E.P.I

RISQUE
D'ENTRAÎNEMENT
MÉCANIQUE

RISQUE DE
COUPURE DE LA
MAIN

PRÉCAUTIONS DE SÉCURITÉ !!!

- Lorsque la machine est en mouvement, il est interdit de mettre les mains dans le broyeur pour éviter iatoute blessure.
- Éviter de mettre trop de plastique d’un coup dans le broyeur car cela peut user le moteur.
- Nettoyez toujours le broyeur après l'avoir utilisé pour broyer un type différent de plastique.
- Dans la benne de récupération, ne pas mélanger différents types de plastique.
- Éloigner les bijoux, les cheveux longs ou les vêtements amples (par exemple, les cravates) de l'ouverture iadu broyeur.
- Ne jamais laisser fonctionner la machine sans surveillance.
- Garder les mains éloignées de toutes pièces en mouvement.
- En cas de dysfonctionnement, actionner le bouton d’arrêt d’urgence.

En cas d’incident, contacter immédiatement le personnel de GINOVA. N’hésitez pas à demander conseil auprès de ces personnes.

# Utilisation du broyeur de plastique

UTILISATION; 1/ Passer le disjoncteur sur ON; 2/ Mettre le bouton 3 positions sur :; aaiiOFF.

PROPRETÉ DU POSTE

En cas d’incident, contacter immédiatement le personnel de GINOVA. N’hésitez pas à demander conseil auprès de ces personnes.

- I (marche avant) pour mettre en route le broyeur
- II (marche arrière) en cas de problème comme dents bloquées

3/ Régler la vitesse de broyage grâce au potentiomètre

4/ Une fois le broyage terminé, mettre le bouton 3 positions sur 0 et remettre le disjoncteur sur

- Assurez-vous avant de partir de laisser le poste de travail dans un état de propreté convenable.
- Si vous changez de plastique à broyer, veillez à ce qu’il ne reste aucun copeaux d’autres type de iaplastique dans le broyeur.

POTENTIAL RISKS

### Utilisation of the shredder

MECHANICAL
RISK

HAND CUTTING
RISK

SECURITY PRECAUTIONS
❖ | When the machine is in motion, putting your hand into the crusher is forbidden to avoid injury.
❖ | Avoid putting too much plastic into the shredder as this can wear down the motor.
❖ | Always clean the shredder after using it to shred a particular type of plastic.
❖ | In the recycling bin, do not mix different types of plastic.
❖ | Keep jewelries, long hair, or loose clothing (i.e., neckties) away from the plastic shredder opening.
❖ | Never leave the machine running unattended.
❖ | Keep hands away from all moving parts.
❖ | Avoid putting hard objects to avoid damaging the blades.
❖ | Regularly lubricate and maintain the running parts.

In the event of an incident, contact GINOVA personnel immediately. Do not hesitate to seek advice from these people.

### Utilisation of the shredder

UTILISATION; 1/ Switch the circuit breaker to ON; 2/ Set the 3-position button to : - ON (forward) to start the grinder.; jammed teeth.; OFF.

CLEANLINESS OF THE STATION

- OFF (reverse) in case of problems such as

In the event of an incident, contact GINOVA personnel immediately. Do not hesitate to seek advice from these people.

3/ Adjust the grinding speed using the potentiometer.

4/ Once the grinding is finished, put the 3-position button on 0 and put the circuit breaker back on

- Make sure before leaving to leave the workstation in a suitable state of cleanliness.
- If you change the plastic to be shredded, make sure that there are no shavings of other types of plastic left in the shredder.

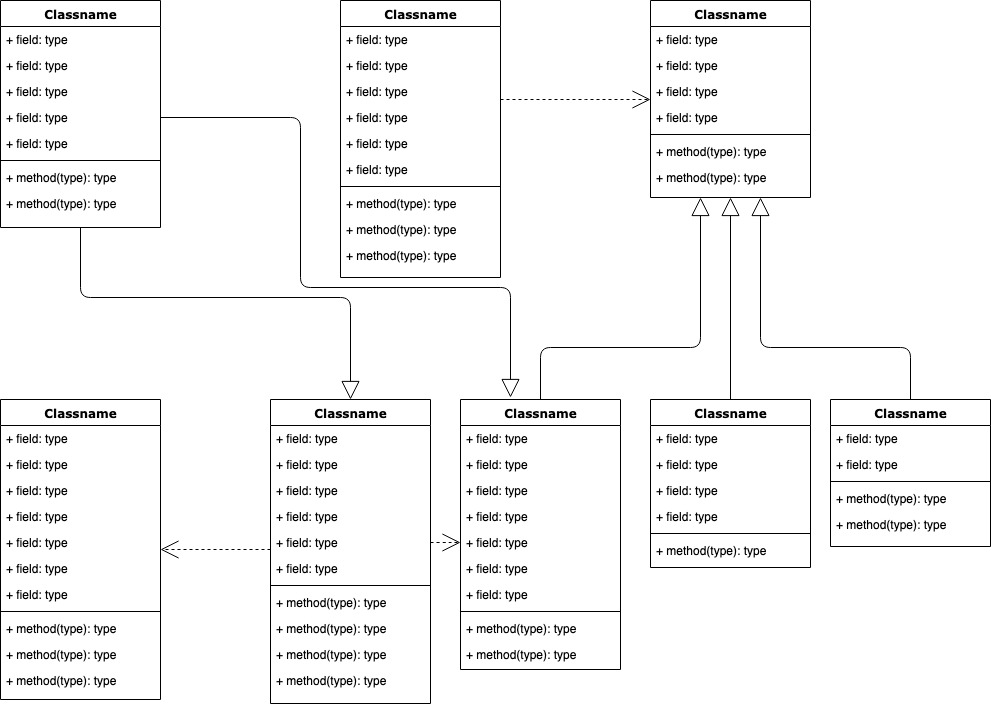
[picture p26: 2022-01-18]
Sources/Images/Template of software architecture.jpg

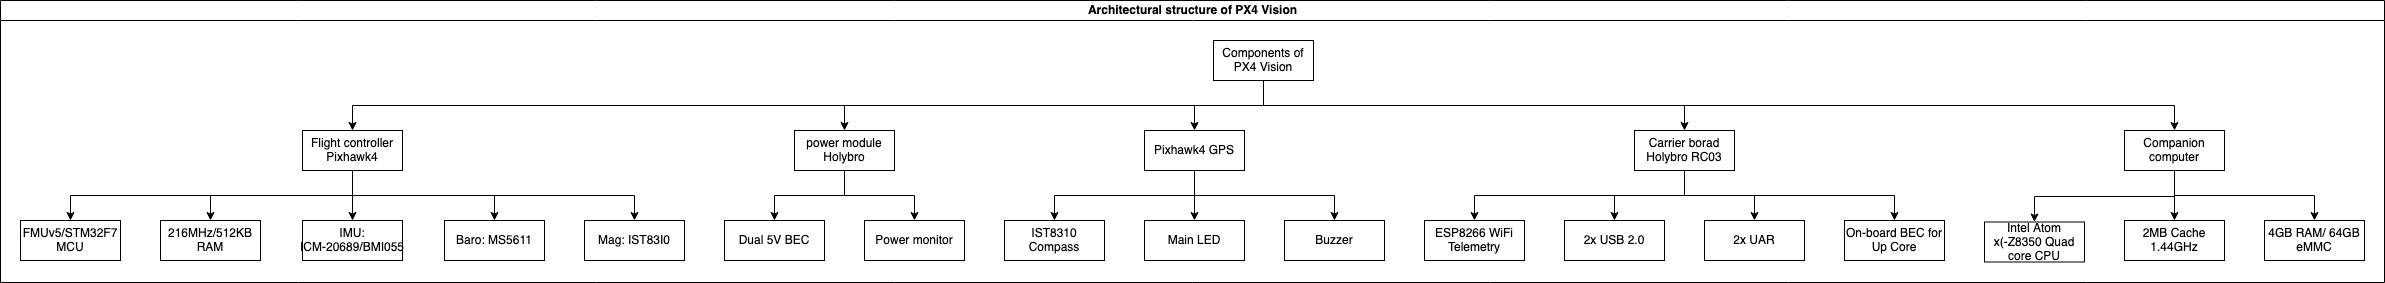
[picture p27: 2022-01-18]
Sources/Images/Architecture of electrical structural model.jpg

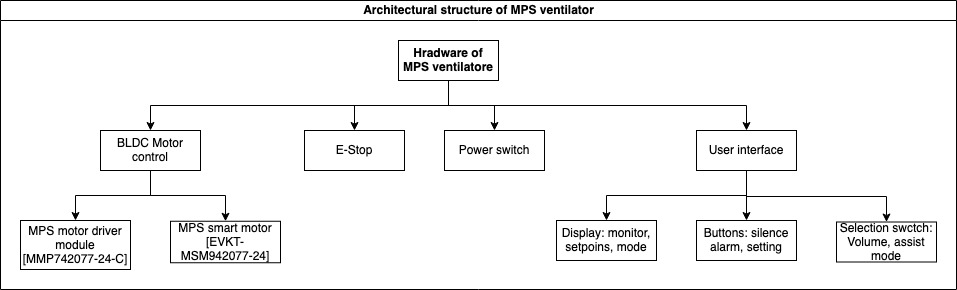
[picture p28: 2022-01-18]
Sources/Images/Architecture of mechanical structural model.jpg

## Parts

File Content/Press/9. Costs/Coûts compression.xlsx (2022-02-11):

Description |  |  |  |  | Material | Details | Quantity | Where to get it | Price | Comments
Machine parts |  |  | Mécanique
 | Oven |  | Four |  |  |  | 1 | Déchetterie Coublevie | 0.00 € | https://www.adepem.com/four/viva/ref/vvh32c3350-20
 |  | ~~Frame (bar)~~ |  | ~~Encadrement (barre)~~ | ~~Steel~~ |  | ~~7~~ | ~~Entrepot du bricolage~~ | ~~16.10 €~~ | ~~https://www.entrepot-du-bricolage.fr/p/pr-corniere-egale-acier-profile-a-froid-15-5-x-15-5-mm-zingue-1-m-alfer-1089646 ~~
 |  | ~~Closing plate~~ |  | ~~Plaque de fermeture~~ | ~~Stainless~~ |  | ~~5~~ | ~~Arc-en-ciel recyclage~~ | ~~30.20 €~~ | ~~Vente leboncoin 10€~~
 |  | Metal plate (inside reinforce) |  | Plaque (renforcer intérieur) | Steel |  | 1 | Arc-en-ciel recyclage | 1.50 €
 |  | Platform |  | Plateforme | Steel |  | 1 | Arc-en-ciel recyclage | 5.00 €
 |  | Shaft |  | Tige | Steel |  |  | Arc-en-ciel recyclage
 |  | Round tube |  | Tube rond | Steel |  |  | Arc-en-ciel recyclage
 | Structure |  | Structure
 |  | Table oven support |  | Table support four | Bois |  | 1 | Cave | 0.00 €
 |  | Board support car jack |  | Planche support cric voiture | Bois |  | 1 | Parents | 0.00 €
 |  | Angle profile board support |  | Profilé angle maintien planche | Steel |  | 1 | Entrepot du bricolage | 2.30 €
 |  | Car jack |  | Cric manuel de voiture | Steel |  | 1 | Casse automobile Brignoud | 10.00 €
 |  | Screws and bolts |  | Visserie | Steel | M8 | 1 | Bricorama | 7.77 €
 |  |  | Évacuation de gaz (méthane et éthylène)
 |  |  |  | plaques contreplaqué | bois | 3mm
 |  |  |  | filtre à charbon actif
 |  |  |  | gaine flexible en alu | alu
Electronics |  |  | Electronique
 | Junction box |  | Boite de dérivation |  |  |  | 1 | Arc-en-ciel recyclage | 1.75 €
 |  | PID controller |  | Régulateur PID |  | REX-C100 |  | https://www.manomano.fr/catalogue/p/rex-c100-ssr-an-ssr-40da-m6-pouces-taille-1-metre-sortie-de-relais-de-thermostat-en-trois-pieces-27777809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 | 20.99 € | https://www.wish.com/product/5ebe0277dcaae00b8aa24d43?from_ad=goog_shopping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
 |  | Static relay |  | Relais statique |  | SSR 40 A
 |  | Thermocouple |  | Thermocouple |  | K - 0-1300°C
 |  |  |  | Câble électrique |  |  | XXX m
 |  |  |  | Câble alimentation |  |  | XXX m
 |  |  |  | Lumière intérieure four
 |  |  | Chauffe plaques
 |  |  |  | Chauffe-futs |  | 40mm/ 50W/ 220V |  | https://fr.rs-online.com/web/p/elements-chauffants/8607139 | 0.00 €
 |  |  |  | Terminal céramique |  | 4 poles |  | https://www.distrelec.fr/fr/terminal-strip-mm-poles-blanc-camdenboss-chtb4-4n/p/14831640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 | 0.00 €
 |  |  |  | laine de verre |  |  | (en m2) | https://www.castorama.fr/rouleau-laine-de-verre-kraft-supralaine-1-2-x-5-4-m-ep-200-mm-vendu-au-rouleau/3596265164894_CAFR.prd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 | #VALUE!
Machining |  |  | Usinage
 | Tools (end pieces screwdriver) |  | Outils (embouts de tournevis) |  |  |  | 1 | Bricorama | 27.05 €
 | Drills |  | Forets |  |  |  | 4 | Bricorama | 9.80 €
 | Discs angle grinder |  | Disques disqueuse |  |  |  | 2 | Entrepot du Bricolage | 5.00 €
 | Welding |  | Soudage |  |  |  |  | Christian Perissier | 10.00 €
 | Chuck key |  | Cle mandrin |  |  |  | 1 | Bricorama | 3.60 €
 | Tools box |  | Boite à outils |  |  |  | 1 | Bricorama | 16.50 €
 | TOTAL |  |  |  |  |  |  |  | #VALUE!

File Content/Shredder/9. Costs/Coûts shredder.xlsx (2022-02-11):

Description |  |  |  |  | Material | Details | Quantity | Where to get it | Price | Comments
Machine parts |  |  | Mécanique
 | 3mm pieces |  | Pièces 3mm |  | Steel |  | 1 | IUT Joseph Fourier - Grenoble | 0.00 €
 | 5mm pieces |  | Pièces 5mm |  | Steel |  | 1 | http://www.oxytemps.fr/ | 133.28 €
 | 6mm pieces |  | Pièces 6mm |  | Steel |  | 1
 |  | Screw |  | Vis | Steel | M6 x ?? | 8 |  | 0.00 €
 |  | Nut |  | Ecrou | Stainless | M6 | 8 |  | 0.00 €
 |  | Washer |  | Rondelle | Stainless | M6 | 8
 | Hexagonal bar |  | Barre hexagonale |  | Steel |  | 1 | https://www.acier-detail-decoupe.fr/aciers-doux/2291-acier-etire-doux-a37.html | 6.92 €
 | Bearing |  | Roulement à billes |  |  | UCFL204 Ø20mm | 2 | https://www.123roulement.com/palier-UCFL204.php | 22.01 €
 |  | Screw |  | Vis tête fraisée | Stainless | M10 x 60 | 4 | Neton | 3.10 €
 |  | Nut |  | Ecrou | Stainless | M10 6 pans | 4 | Neton | 2.17 €
 | Threaded shaft |  | Tige filetée |  | Steel | Ø10 - 25cm | 2 | Mon brico | 1.95 € | 1m Ø10
 |  | Nut |  | Ecrou | Stainless | M10 6 pans | 4
 | Motor/Shaft connector |  | Adaptateur moteur/tige |  | Steel | Ø60mm L60mm | 1 | https://www.acier-detail-decoupe.fr/aciers-carb/4921-acier-lamine-xc48-c45.html | 2.50 €
 |  | Screw |  | Vis | Stainless | M8 x ?? | 2 |  | 0.00 €
 | Structure |  | Structure |  | Steel |  | 1 | Ancien portail | 0.00 € | Mettre axe moteur et broyeur au même niveau
 | Angle profile |  | Profilé angle droit |  | Steel | 30*30*3mm | 2 |  | 0.00 € | Fixer le broyeur à la structure
 |  | Washer |  | Rondelle | Stainless | M10 | 16 |  | 0.00 € | Mettre axe moteur et broyeur au même niveau
 |  | Screw/Shaft |  | Vis/Tige filetée | Stainless | M10 x 50 | 4 |  | 0.00 €
 |  | Nut |  | Ecrou | Stainless | M10 | 8 |  | 0.00 €
 | Screw |  | Vis |  | Stainless | M8 x ?? | 3 |  | 0.00 €
 | Nut |  | Ecrou |  | Stainless | M8 | 3 |  | 0.00 €
 | Washer |  | Rondelle |  | Stainless | M8 | 3 |  | 0.00 €
 | Mesh sheet |  | Feuille de maille / tôle perforée |  | Steel | 1<Ep<2mm | 1 | Arc-en-ciel | 0.50 € | https://www.leroymerlin.fr/v3/p/produits/tole-acier-metal-deploye-brut-gris-l-25-x-l-50-cm-ep-1-2-mm-e19276
 | Sheet metal for hopper |  | Métal pour tremie |  | Steel | 1<Ep<2mm | 2 | https://www.leroymerlin.fr/produits/quincaillerie/corde-chaine-cable-tole-fer-et-profile/tole/tole-acier-lisse-brut-gris-l-60-x-l-100-cm-ep-1-5-mm-69954311.html | 35.20 €
 | Plastic filament |  | Filament plastique |  | Plastic | 200 gr |  |  | 10.00 €
 |  |  | Chariot support |  |  |  | 1 |  | récup
Gear Motor |  |  | Moto réducteur
 | Engine |  | Moteur |  |  |  | 1 | https://fr.rs-online.com/web/p/moteurs-a-courant-alternatif/1879870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 | 373.30 €
 | Gearbox |  | Réducteur |  |  |  | 1 | https://www.motovario.com/fra/produits/reducteurs-coaxiaux--serie-h/reducteurs-coaxiaux--aluminium | 500.00 €
 | Coupling |  | Accouplement |  |  | d = 56mm, l = 78mm | 1 | https://fr.rs-online.com/web/p/accouplements/8087301 | 47.66 €
Electronics |  |  | Electronique
 | 3 Poles male plug + Earth |  | Prise mâle 3 Pôles + Terre |  |  |  | 1 | https://www.leroymerlin.fr/v3/p/produits/fiche-electrique-male-3-poles-terre-20-a-legrand-e29610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 | 14.75 €
 | 3-position switch contactor |  | Interrupteur 3 positions contacteur |  |  | on-off-on 15A/250V | 1 | https://www.manomano.fr/p/interrupteur-commutateur-contacteur-bouton-a-bascule-noir-dp3t-on-off-on-15a-250v-3-positions-6458399 | 7.32 €
 | Female flat terminal |  | Cosse plate femelle |  |  | 6,3 x 0,8mm | 6 |  | 0.00 €
 | Electrical Cable |  | Câble électrique |  |  |  |  |  | 0.00 €
 | Electronic box |  | Boite de jonction |  |  |  |  |  | 0.00 €
 | ~~Permanent capacitor~~ |  | ~~Condensateur permanent~~ |  |  | ~~20 µF à câble~~ | ~~1~~ | ~~https://www.condensateur-web.fr/condensateur-permanent-20-micro-f-a-cable-A45.html https://www.astuces-pratiques.fr/electronique/couplage-etoile-ou-triangle-moteur-asynchrone~~ | ~~10.32 €~~ | ~~Dépend de la puissance du moteur - 230V~~
 | End-stop sensor |  | Capteur end-stop |  |  |  | 1 | https://fr.rs-online.com/web/p/capteurs-photoelectriques/2024447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 | 24.23 €
 | Yellow LED flashing light |  | Gyrophare Led Jaune |  |  | 24 V CA CC -IP 65 | 1 | https://www.se.com/be/fr/product/XVBL0B8/balise-feu-fixe-jaune-xvb-del-intégrée-24-v-ca-cc-ip-65/?range=644-harmony-xvb&selected-node-id=12144412688 | 225.15 €
 | Emergency stop button |  | Bouton d'arret d'urgence |  |  |  | 1 | https://fr.rs-online.com/web/p/boutons-arret-durgence/2195813 | 23.60 €
 | Potentiometer |  | Potentiomètre |  |  |  | 1 |  | 10.00 €
 | Circuit breaker |  | Disjoncteur |  |  | 2 poles C60N | 1 | https://fr.rs-online.com/web/p/disjoncteurs/2142066?matchtype=&aud-827186183926:pla-389498239585&gclsrc=aw.ds | 81.68 €
 | Converter |  | Convertisseur |  |  |  | 1 | https://fr.rs-online.com/web/p/variateurs-de-frequence-et-de-vitesse/8226241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 | 377.36 €
Machining |  |  | Usinage
 | Screw head |  | Têtes de vis |  |  |  |  | GENOVA Phiphi | 0.00 € | Rajouter sur les plans
 | Bearing spacer 3mm |  | Entretoise roulement 3mm |  | Plexiglass |  |  | GENOVA Phiphi | 0.00 € | Ne pas oublier
 | Hexagonal bar |  | Barre hexagonale |  |  |  |  | GENOVA Phiphi | 0.00 € | Tournage
 | Motor/Bar connector |  | Adaptateur moteur/barre |  |  |  |  | GENOVA Phiphi | 0.00 € | Tournage + perçage
 | Drilling Motor/Bar/Connector |  | Perçage Moteur/Barre/Adaptateur |  |  |  |  |  | 0.00 € | Perçage (Forets)
 | Tapping (Thread) |  | Taraud M8 + Foret métal 6,8 |  |  |  |  | Mon Brico | 21.25 € | Taraudage
 | Grinding structure |  | Meuler structure |  |  |  |  |  | 0.00 € | Meulage (Disques)
 | Welding structure |  | Soudage structure |  |  |  |  | Remorque mandrinoise | 50.00 € | Soudage
 | Water jet cutting hopper |  | Découpe jet d'eau trémie |  |  |  |  | ENSE3 Fablab | -
 | Hopper folding |  | Pliage trémie |  |  |  |  | GInova | -
 | 3D printing |  | Impression 3D |  |  |  |  | FavLab | -
Finishing |  |  | Finitions
 | Sanding + Disc |  | Ponçage + disques |  |  |  |  |  | 0.00 €
 | Machine costs: |  | Coûts machines:
 |  | Water jet cutting |  | Découpe jet d'eau |  |  | 20min |  | 4.00 €
 |  | 3D printer |  | Imprimante 3D |  |  | 2h |  | 1.30 €
 |  | lathe |  | tour |  |  | 20min |  | 16.00 €
 | Operator costs |  | Coûts opérateur |  |  |  | 1h20 (trémis découpe + pliage + tour) |  | 40.00 € | taux horaire opérateur = 30€
 | Rustproof paint |  | Peinture anti-rouille |  |  |  |  |  | 14.50 €
 | TOTAL |  |  |  |  |  |  |  | 2060.05 €

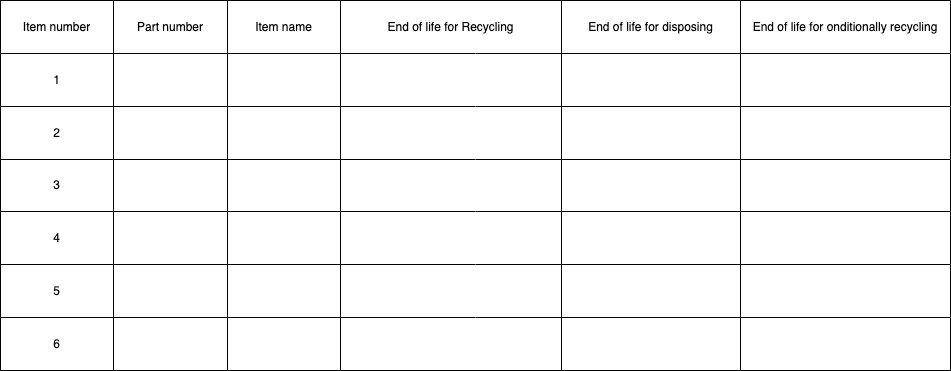
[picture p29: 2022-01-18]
Sources/Images/End of life of product and components .jpg

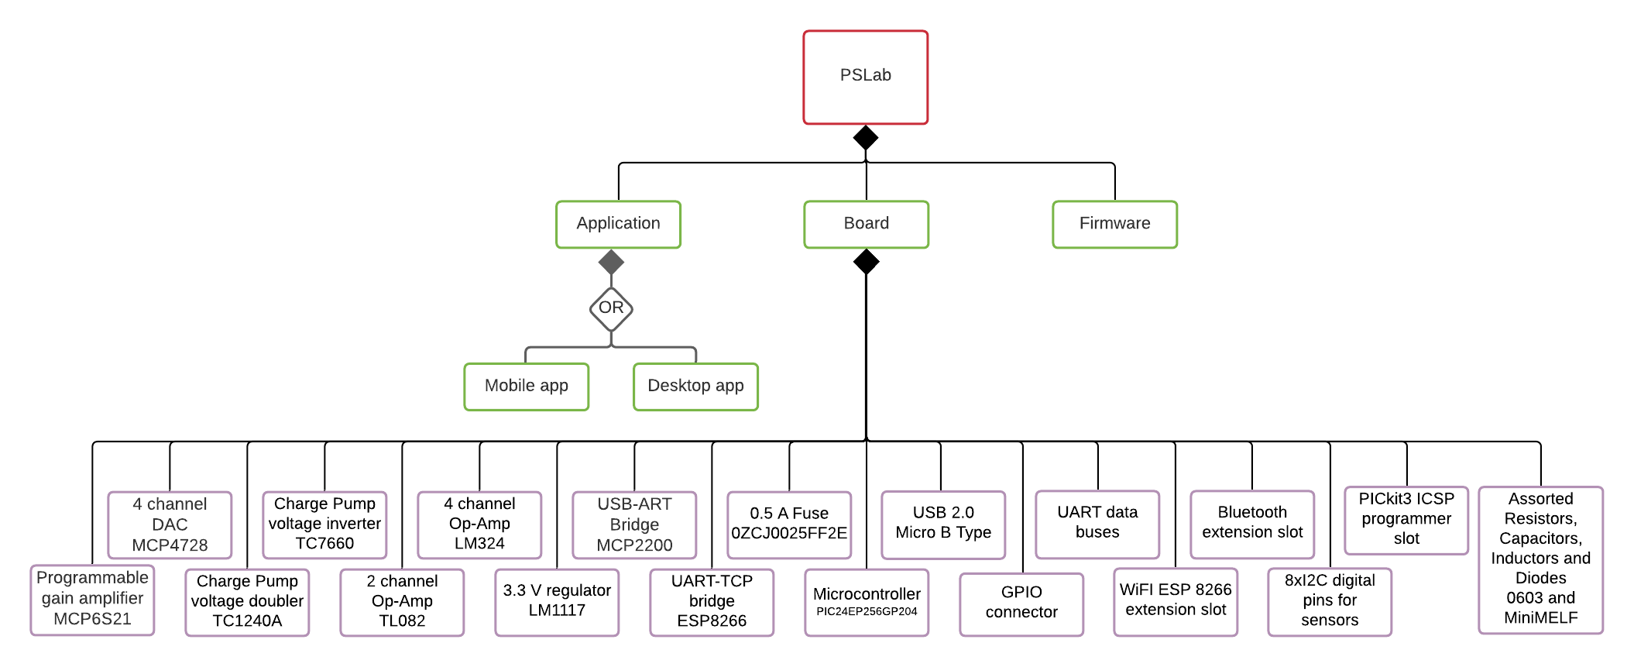
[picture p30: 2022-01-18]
Sources/Images/BOM.png

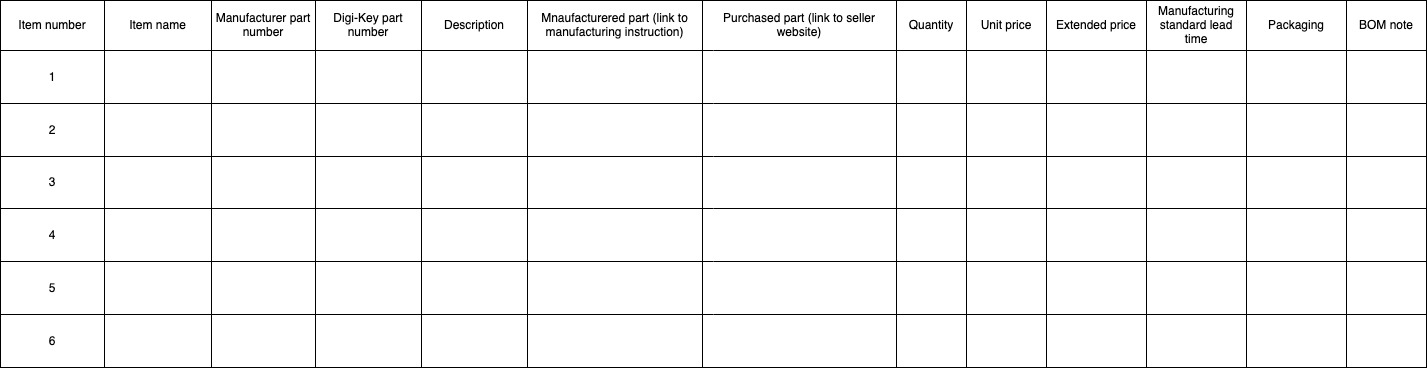
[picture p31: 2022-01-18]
Sources/Images/BOM template-2.jpg

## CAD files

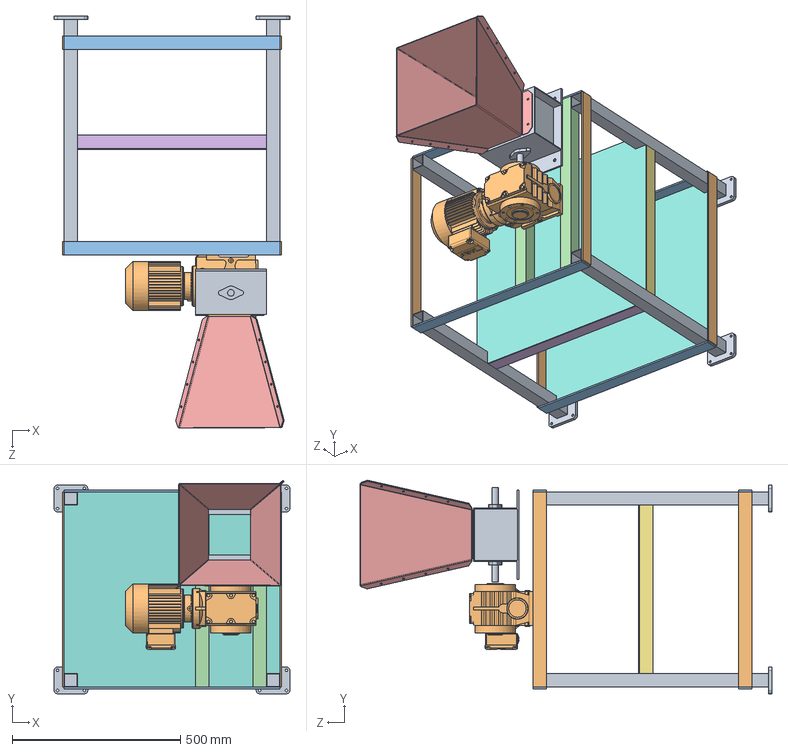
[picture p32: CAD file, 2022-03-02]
Content/Shredder/3. Design/CAD/Assemblage1.SLDASM
700.0 x 634.4 x 1223.4 mm
PIED x 4
RENFORT_largeur x 4
RENFORT_longueur x 4
580mm 40x40 x 2
Trémie x 2
560mm 40x40 x 2
500mm 40x40 x 2
WorkbenchV x 2
Shredder
SEW SA57DZ71C4

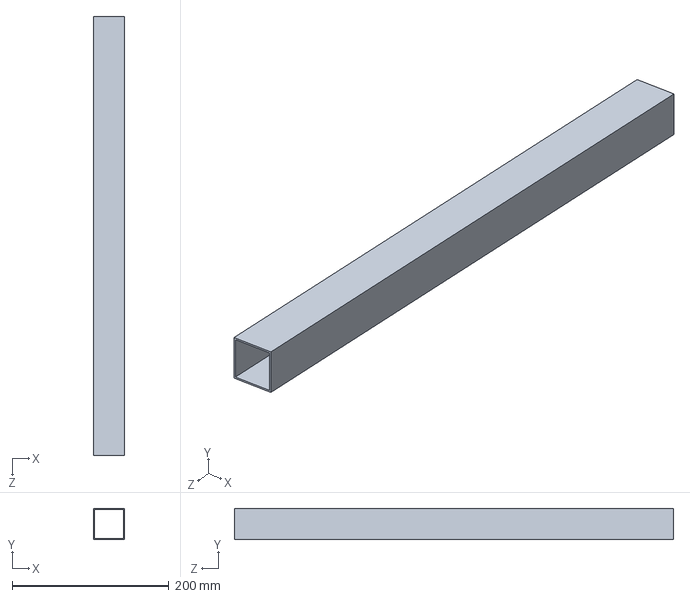
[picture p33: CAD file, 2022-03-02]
Content/Shredder/3. Design/CAD/560mm 40x40.SLDPRT
40.0 x 40.0 x 560.0 mm

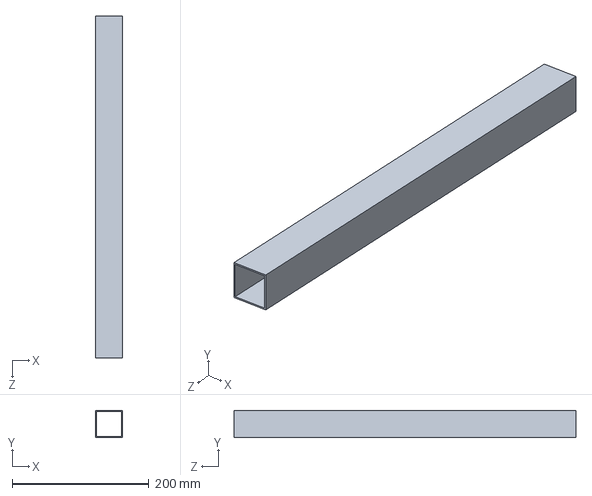
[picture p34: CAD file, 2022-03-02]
Content/Shredder/3. Design/CAD/500mm 40x40.SLDPRT
40.0 x 40.0 x 500.0 mm

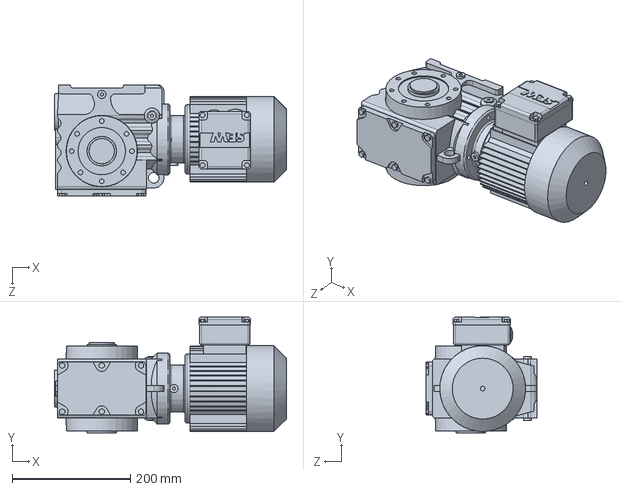
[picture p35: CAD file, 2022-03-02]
Content/Shredder/3. Design/CAD/SEW SA57DZ71C4.SLDPRT
392.5 x 196.0 x 188.0 mm

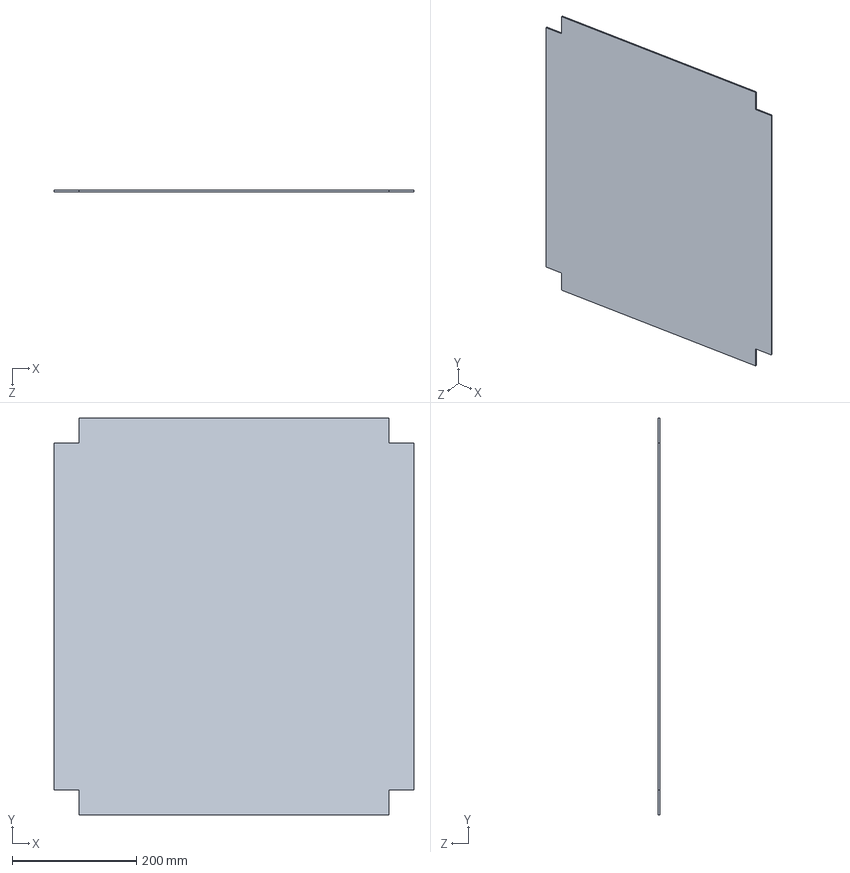
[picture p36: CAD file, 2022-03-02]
Content/Shredder/3. Design/CAD/WorkbenchV.SLDPRT
580.0 x 640.0 x 3.00 mm

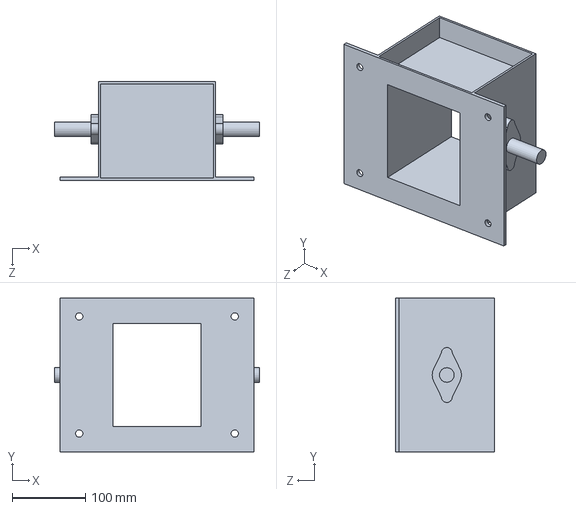
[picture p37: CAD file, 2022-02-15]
Content/Shredder/3. Design/CAD/Shredder.SLDPRT
280.0 x 210.0 x 135.0 mm

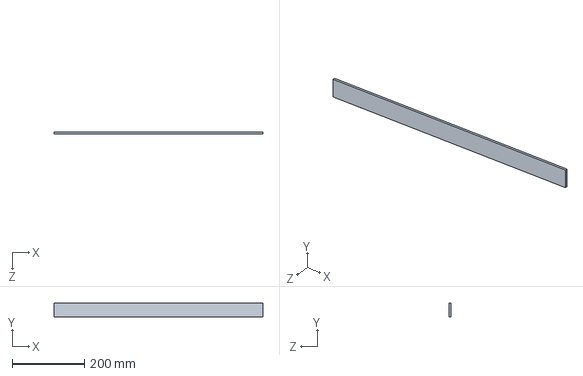
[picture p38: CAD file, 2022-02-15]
Content/Shredder/3. Design/CAD/RENFORT_largeur.SLDPRT
580.0 x 40.0 x 5.00 mm

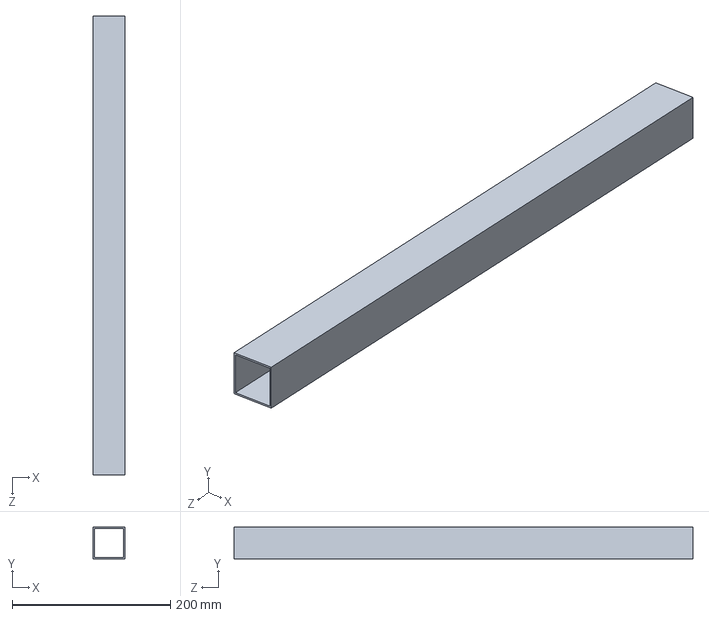
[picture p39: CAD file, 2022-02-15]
Content/Shredder/3. Design/CAD/580mm 40x40.SLDPRT
40.0 x 40.0 x 580.0 mm

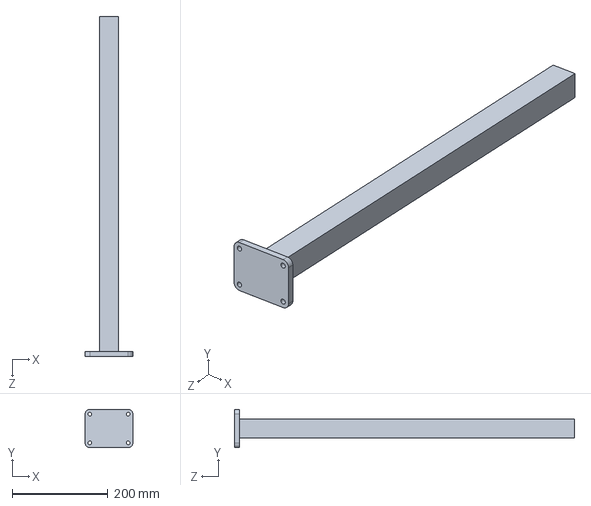
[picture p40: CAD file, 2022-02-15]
Content/Shredder/3. Design/CAD/PIED.SLDPRT
100.0 x 80.0 x 710.0 mm

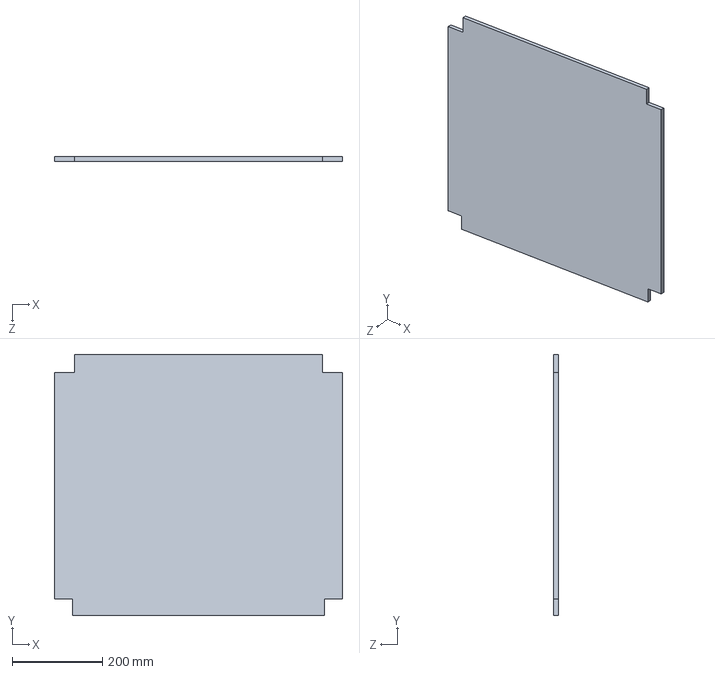
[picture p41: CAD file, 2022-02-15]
Content/Shredder/3. Design/CAD/Workbench.SLDPRT
640.0 x 580.0 x 10.0 mm

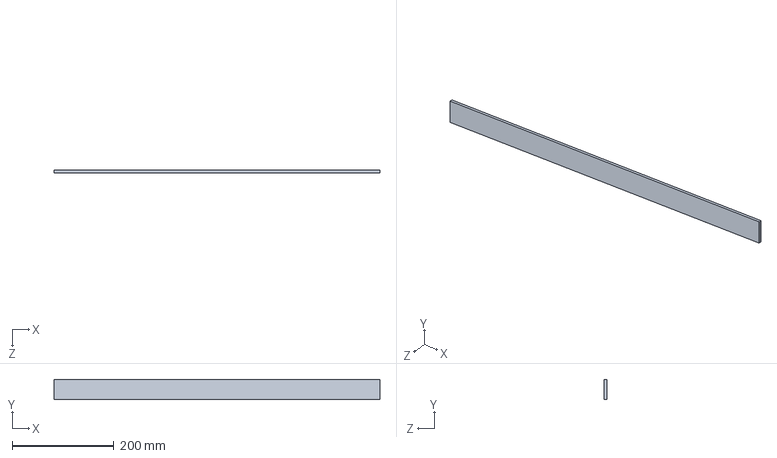
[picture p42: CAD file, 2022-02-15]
Content/Shredder/3. Design/CAD/RENFORT_longueur.SLDPRT
640.0 x 40.0 x 5.00 mm

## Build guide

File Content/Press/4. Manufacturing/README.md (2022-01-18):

# **Manufacturing**

*I would like to enable makers to understand the process by which raw materials transform into a final product.*

## **How to document a manufacturing process?**

*Manufacturing instructions can guide the makers to follow a process for replicating a product. Manufacturing instructions mean full description and instructions concerning raw material, operating conditions, and process to be employed for the manufacture and assembly of the product.
The bill of material (BOM) is the document that describes all the components and their references. If the component is to be purchased one should find all the information required to buy the part. If the part is to be manufactured one should find all the descriptions of the manufacturing instructions as described below.* 

## **How to document a manufacturing process part?**

*If the part is to be manufactured one should find all the descriptions of the manufacturing instructions as described below.* 

### *1. Bill of material (BOM)*
<details>
  <summary>Click to see the guideline</summary>
 
 - **Definition:** *A bill of materials (BOM) is a comprehensive list of parts, items, and other materials required to create a product, as well as instructions required for gathering and using the required materials.*

```
What should include the bill of material (not limited to...)?

   1. Part number
   2. Item name
   3. Manufacturer part number
   4. Digi-Key part number
   5. Description
   6. Manufactured part (link to manufacturing instruction)
   7. Purchased part (link to seller website)
   8. Quantity
   9. Price
   10. Manufacturing standard lead time
   11. Packaging
   12. BOM notes
   13. ...
   ```
</details>

<details>
  <summary>Click to see the example</summary>
 
 #### *Example 1: [JPL Open Source Rover](https://github.com/nasa-jpl/open-source-rover/tree/master/bill_of_materials)*
  


*BOM of JPL open-source Rover*
  
 #### *Example 2: [SatNOGS Rotator v3](https://gitlab.com/librespacefoundation/satnogs/satnogs-rotator/blob/master/rotator-bom.ods)*
  
 #### *Example 3: [Krab v1.0](https://projects.fablabs.io/@avishek/krab-v10)*

</details>

### BOM Template

 #### Bill of material
 
 *You can use this template on the App diagram to define the bill of material of your project/product.*

image of BOM

 <a href="https://app.diagrams.net/#Hamerezoji1362%2Fdrawio-github%2Fmaster%2FBOM%20template.drawio" target="_blank">Edit As New</a> | <a href="https://app.diagrams.net/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">Edit in diagrams.net</a>
 
  ### *2. Manufacturing instructions should include:*
 
 #### *2.1. Manufacturing tools*
  <details>
  <summary>Click to see the guideline!</summary>
 
  - **Definition:** *It means all the machinery, equipment, and processes used to manufacture products. Manufacturing technology guide to find the type of necessary technology to produce the part. In that case, it should describe the most suitable technology according to the context.*

 ```
 What should include the documentation of manufacturing tools?
 
 Type of machines used 

   1. CNC machine tools for machining metal or other rigid materials
     - Milling 
     - Lathe
     - Cutting 
     - Drilling 
     - Etc.
    
   2. Other common manufacturing tools
     - 3D printing (FDM, SLS...) 
     - Thermoforming
     - Burning machining technology (laser cutting, Plasma cutting, ...) 
     - Bonding technologies (Solder, cold welding, arc welding, adhesive bonding ...)  
  
   3. Finishing: to achieve the right properties such as surface quality, geometrical accuracy, and mechanical properties, finishing is essential. 
     - Sanding after 3D printing
     - Gap filling
     - Blasting
     - Polishing
     - Priming and painting
     - Etc.
  
 How to visualize the manufacturing tools? 
  1. Images 
  2. Videos  
 ```
 </details>
 
  <details>
  <summary>Click to see the examples!</summary>
 
   #### *Example 1:* [JPL Open Source Rover](https://github.com/nasa-jpl/open-source-rover/tree/master/mechanical/body_assembly#3-machiningfabrication)
   
   #### *Example 2:* [SatNOGS Rotator v3](https://wiki.satnogs.org/SatNOGS_Rotator_v3#Build_Sequence) 
  </details>
 
   #### Template of Manufacturing tools
   
*You can use this template on the App diagram to define manufacturing tools.*
 
image of Manufacturing tools

 <a href="https://app.diagrams.net/#Hamerezoji1362%2Fdrawio-github%2Fmaster%2FManufacturing%20technology.drawio">Edit As New</a> | <a href="https://app.diagrams.net/#Hamerezoji1362%2Fdrawio-github%2Fmaster%2FManufacturing%20technology.png">Edit in diagrams.net</a>

 #### *2.2. Manufacturing sequences and instructions*
 <details>
  <summary>Click to see the guideline!</summary>
 
  - **Definition:** *Manufacturing sequences refer to step-by-step machining and manufacturing processes in a target-oriented arrangement to enable manufacturing.*
  
  - **Comments:**
  
      * The machining sequence should define for the manufacturing of each part.
      * Process parameters are all those parameters that are inherent to any machining operation and should have a suitable finite value to smooth and efficient removal of materials.
      * Manufacturing standard file formats support some of the manufacturing processes and the surface geometry of a design without the possibility of modification.

```
What does include the documentation of manufacturing sequences and instructions?
 
  1. Name of the related machine of each step
  2. Describing step by step sequence of the machining process
    - Machine
    - Type of operation
    - Tools description 
    - Process parameters of each machining operation ( refer to the template of manufacturing sequences below)
       - Process parameters of 3D printing
       - Process parameters of Laser cutting
       - Process parameters of CNC machines such as Lathe, Milling, etc.
       - Process parameters of arc welding
    - Raw material
    - Manufacturing files (STL, SVG or G-code, ...)
       - CAD files in an interchange format such as STL that is suitable for 3D printing 
       - Nominal geometry and its allowable variation by using symbolic language on 2D drawings like SVG, JPEG, and PDF format that is suitable for laser cutting
       - Manufacturing export formats such as G-code, STEP-NC is suitable for CNC machining
       - Circuit board design formats such as Gerber RS-274X, excellon that is suitable for vector photoplotters 2D mechanical NC machines
  ``` 
</details>

 <details>
  <summary>Click to see the examples!</summary>
 
   #### *Example 1:* [JPL Open Source Rover](https://github.com/nasa-jpl/open-source-rover/tree/master/mechanical/body_assembly#3-machiningfabrication)
  
   #### *Example 2:* [DIY Dremel CNC design and parts](https://www.thingiverse.com/thing:3004773) and [its CAM file for machining](https://www.estlcam.de/) 
  
   #### *Example 3:* This table shows an example of the manufacturing sequences.
  
  image of machining sequences
  
  #### *Example 4:* [SatNOGS Rotator v3](https://wiki.satnogs.org/SatNOGS_Rotator_v3#Specifications), [2D drawing file](https://wiki.satnogs.org/File:C1001.png)
  
  #### *Example 5:* Types of CAD format of [transmagic](https://transmagic.com/cad-formats/)
   </details>
  
  #### Template of manufacturing sequences
  
   *You can use these parameters for each machining operation to complete the manufacturing sequences on the App diagram.*
  
  #### 1. 3D printer parameters 

   * Extruder setting 
      * Extrusion multiplier
      * Retraction distance 
      * Retraction speed 
      * Coasting
   * Layer setting
      * First layer height
      * First layer speed
   * Laver height
   * Printing bed temperature
   * Infill setting
      * Internal/Eternal fill pattern
   * Temperature setting
   * Cooling setting
     
  #### 2. CNC machines parameters such as Lathe, Milling, etc. 
  
   * Cutting parameters
      * Cutting speed
      * Feed rate
      * Cutting depth
      * Cutting width
      * Cutting force
      * Spindle speed
      * Cutting temperature
   * Cutting tool
      * Tool Geometry
      * Tool setting
   * Coolant 
      
 #### 3. Burning machining parameters such as laser cutting 
  
   * Beam parameters
      * Wavelength
      * Power and intensity 
      * Polarization
   * Process Parameters
      * Focusing of laser beams (the focal length of the lens)
      * Focal position
      * Angle of incidence
      * Cutting speed
      * Gas pressure
      * Stand-off distance
      * Expected duration

  #### 4. Bonding technologies parameters such as Arc welding
    
   * Welding current
   * Welding voltage
   * Arc travel speed
   * Torch angle
      * Longitudinal
      * Transverse
   * Electrode force
   * Electrode diameters
   * Length of arc
   
image of manufacturing sequence

 <a href="https://app.diagrams.net/#Hamerezoji1362%2Fdrawio-github%2Fmaster%2FMachining%20parameters.drawio">Edit As New</a> | <a href="https://app.diagrams.net/#Hamerezoji1362%2Fdrawio-github%2Fmaster%2Fmachnining%20paramters.png">Edit in diagrams.net</a>

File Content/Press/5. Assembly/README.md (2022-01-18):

# **Assembly**

*I would like to enable makers to understand the steps of constructing a finished product from components or partially compiled units.* 

## **How to document an assembly or disassembly process?**

*Assembly instruction can guide the makers to follow the process of assembly or disassembly of components of a product.*

### **Assembly instructions** 
<details>
  <summary>Click to see the guideline!</summary>
 
 - **Definition:** *Assembly instructions could illustrate visually and with words and text how to assemble or disassemble the mechanical and electrical components of the product.*

 ```
What does include the content of assembly instruction? 

 1. Required skills for assembly
    - Operate drilling machine
    - Operate Band Saw/Dremel
    - Etc.
 2. List of the tools for assembly or disassembly
    - Mandatory
       - Allen Keyset
       - Imperial wrench set
       - Etc.
    - Optional
       - Drill press
       - Etc. 
 3. Assembly sequence
    - Part list for mechanical parts: is a complete list of all parts needed to build the complete product(refer to the BOM at manufacturing section)
       - Item numbers: are based on the assembly structure, that is, the order in which parts are displayed in assembly.
       - Part number or drawing number: which is a reference back to the detail drawing (refer to the BOM). 
       - Description: is usually a part name or a complete description of parts.
       - Quantity is the number of that particular part used on this assembly. 
       - Image of each part
    - Datasheet of components for electronic parts
       - Description of features
          - Core
          - Memories
          - Advanced connectivity
          - etc.
       - Device summary
          - Reference
          - Part number 
       - How to use the parts?
    - Describing the machining/ fabrication if it is necessary during the assembly (refer to manufacturing and see the template below)
      - Machine used
      - Sequence of process 
    - The set of steps necessary to properly assemble the parts
       - Description of the assembly at each step
       - Identifying the joining technology at each step
          - Screwing
          - Bolting
          - Soldering
          - Etc.
  
How to visualize the assembly or disassembly process?
 1. Images 
 2. Videos 
```  
</details>

<details>
  <summary>Click to see the example!</summary>
 
*Some examples of open-source projects that include assembly instructions.*

#### *Example 1:* [Poppy Robot](https://docs.poppy-project.org/en/assembly-guides/ergo-jr/mechanical-construction.html)

#### *Example 2:* [JPL Open Source Rover](https://github.com/nasa-jpl/open-source-rover/tree/master/mechanical/body_assembly)

#### *Example 3:* [SatNOGS Rotator v3](https://wiki.satnogs.org/SatNOGS_Rotator_v3#Assembly) , [Assembly instructions](https://ohai.satnogs.org/project/satnogs-rotator-v3-mechanical-assembly/hardware/) 
  
#### *Example 4:* [Open Source Powered Prosthetic Leg](https://www.hackster.io/open-source-bionics/open-source-powered-prosthetic-leg-56be8e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)
</details>

### Template of assembly
 
 #### 1. Required skills for assembly
 
 *You can use this template on the App diagram to define the required skills for assembly.*
 
image of required skills

 <a href="https://app.diagrams.net/#Hamerezoji1362%2Fdrawio-github%2Fmaster%2FRequired%20skills.drawio">Edit As New</a> | <a href="https://app.diagrams.net/#Hamerezoji1362%2Fdrawio-github%2Fmaster%2FRequired%20skills.png">Edit in diagrams.net</a>

 #### 2. List of the tools for assembly or disassembly
   * Mondatory
     * ...
   * Optional
     * ... 
 #### 3. Assembly sequences 
   * Part list (refer to [Bill of Material (BOM)](https://github.com/OPEN-NEXT/WP2.3-Guideline-and-templatefor-documentation-of-OSH-design-reuse/tree/main/Documentation/4.%20Manufacturing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))
   * Datasheet
  
   *You can use this template on the App diagram to define the part list.*
 
image of partlist

 <a href="https://app.diagrams.net/#Hamerezoji1362%2Fdrawio-github%2Fmaster%2FPart%20list%20or%20data%20sheet.drawio">Edit As New</a> | <a href="https://app.diagrams.net/#Hamerezoji1362%2Fdrawio-github%2Fmaster%2FPart%20list%20or%20data%20sheet.png">Edit in diagrams.net</a>
 
   *You can use this template on the App diagram to define the datasheet.*
 
image of datasheet

 <a href="https://app.diagrams.net/#Hamerezoji1362%2Fdrawio-github%2Fmaster%2FData%20sheet.drawio">Edit As New</a> | <a href="https://app.diagrams.net/#Hamerezoji1362%2Fdrawio-github%2Fmaster%2FData%20sheet.png">Edit in diagrams.net</a>
 
  * Describing the machining/ fabrication of parts if it is necessary (refer to [manufacturing](https://github.com/OPEN-NEXT/wp2.3_Guideline-for-documentation-of-OSH-design-reuse/tree/main/Documentation/4.%20Manufacturing/Manufactured%20workpiece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))
  
 *You can use this template  on the App diagram to demonstrate the components and the process of machining/ fabrication.*
 
image of machining/fabrication

 <a href="https://app.diagrams.net/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">Edit As New</a> | <a href="https://app.diagrams.net/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">Edit in diagrams.net</a>
   
   * The set of steps necessary to properly assemble the parts
   
   *See the example 1 and 2.*
     
   *You can use this template on the App diagram to explain the set of stages for the assembly of the parts.*
 
image of steps to assemble

 <a href="https://app.diagrams.net/#Hamerezoji1362%2Fdrawio-github%2Fmaster%2FSteps%20to%20assemble%20the%20parts.drawio">Edit As New</a> | <a href="https://app.diagrams.net/#Hamerezoji1362%2Fdrawio-github%2Fmaster%2FSteps%20to%20assemble%20the%20parts.png">Edit in diagrams.net</a>

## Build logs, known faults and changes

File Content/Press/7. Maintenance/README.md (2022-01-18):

# **Maintenance**

*I would like to enable makers to understand the process of modifying a system or component after delivery to correct faults, improve performance or other attributes, or adapt to a changing environment.*

## **How to document the maintenance?** 

*Maintenance instructions provide the necessary information to maintain the system effectively and perform the required operations to system works properly in the long run. This includes advice on the frequency of the maintenance and the risks of failure.*

 ### **Maintenance instructions** 
<details>
  <summary>Click to see the guideline!</summary> 
 
  - **Definition:** *A maintenance instruction is a technical communication document intended to give recommendations and necessary information to maintain the system effectively.*

  ```
What does include the documentation of maintenance instructions? 

1. Introduction of general maintenance of the product or system
    - Cleaning
    - Lubricating
    - Regular inspections or services. These can be carried out on a time-based schedule or a usage-based schedule.
       - Maintenance according to predetermined intervals 
       - Maintenance according to prescribed criteria
       - Maintenance by integrating analysis, measurement, and periodic test activities 
    - Regular adjusting machinery if it's necessary
    - Maintenance tools
       - Various tools necessary to perform the maintenance operation
2. Identifying the defective components
    - The equipment performance monitoring   
    - How to detect a defective component
    - Fault elimination
    - Verification of fault elimination
3. Repairing the defective components
    - Step-by-step procedures describing the repairing sequence 
    - Refer to the manufacturing section where you can find the manufacturing instructions to rebuild the defective components
    - Verification of repair
    - Required tools for repairing
4. Replacing equipment components according to the schedule
    - Step-by-step procedures describing the replacing sequence
    - Required tools for replacing the components

How to visualize the process of maintenance?
 1. Images 
 2. Videos 

```
</details>

<details>
  <summary>Click to see the example!</summary>

#### *Example 1:* [FarmBot Genesis V1.5](https://genesis.farm.bot/v1.5/Extras/maintenance)
</details>

### Template of maintenance
 
 #### 1. General maintenance of the product or system
 
   *You can use this template on the App diagram to explain the general maintenance.*
 
image of general maintenance

 <a href="https://app.diagrams.net/#Hamerezoji1362%2Fdrawio-github%2Fmaster%2FGeneral%20maintenance.drawio">Edit As New</a> | <a href="https://app.diagrams.net/#Hamerezoji1362%2Fdrawio-github%2Fmaster%2FGeneral%20maintenance.png">Edit in diagrams.net</a> 
 
 #### 2. Identifying the defective components 
 
 *You can use this template on the App diagram to identify the defective components.*
 
image of defective components

 <a href="https://app.diagrams.net/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">Edit As New</a> | <a href="https://app.diagrams.net/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">Edit in diagrams.net</a>
 
 #### 3. Repairing the defective components

  *You can use this template on the App diagram to describe the repairing process of defective components.*
 
image of repariring the defective components

 <a href="https://app.diagrams.net/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">Edit As New</a> | <a href="https://app.diagrams.net/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">Edit in diagrams.net</a>
 
 #### 4. Replacing equipment components on a schedule

  *You can use this template on the App diagram to describe the replacing procedure of components.*
 
image of replacing components

 <a href="https://app.diagrams.net/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">Edit As New</a> | <a href="https://app.diagrams.net/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">Edit in diagrams.net</a>

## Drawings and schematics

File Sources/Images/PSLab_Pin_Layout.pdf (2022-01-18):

# Pocket Science Lab V5

# Pin Layout Diagram

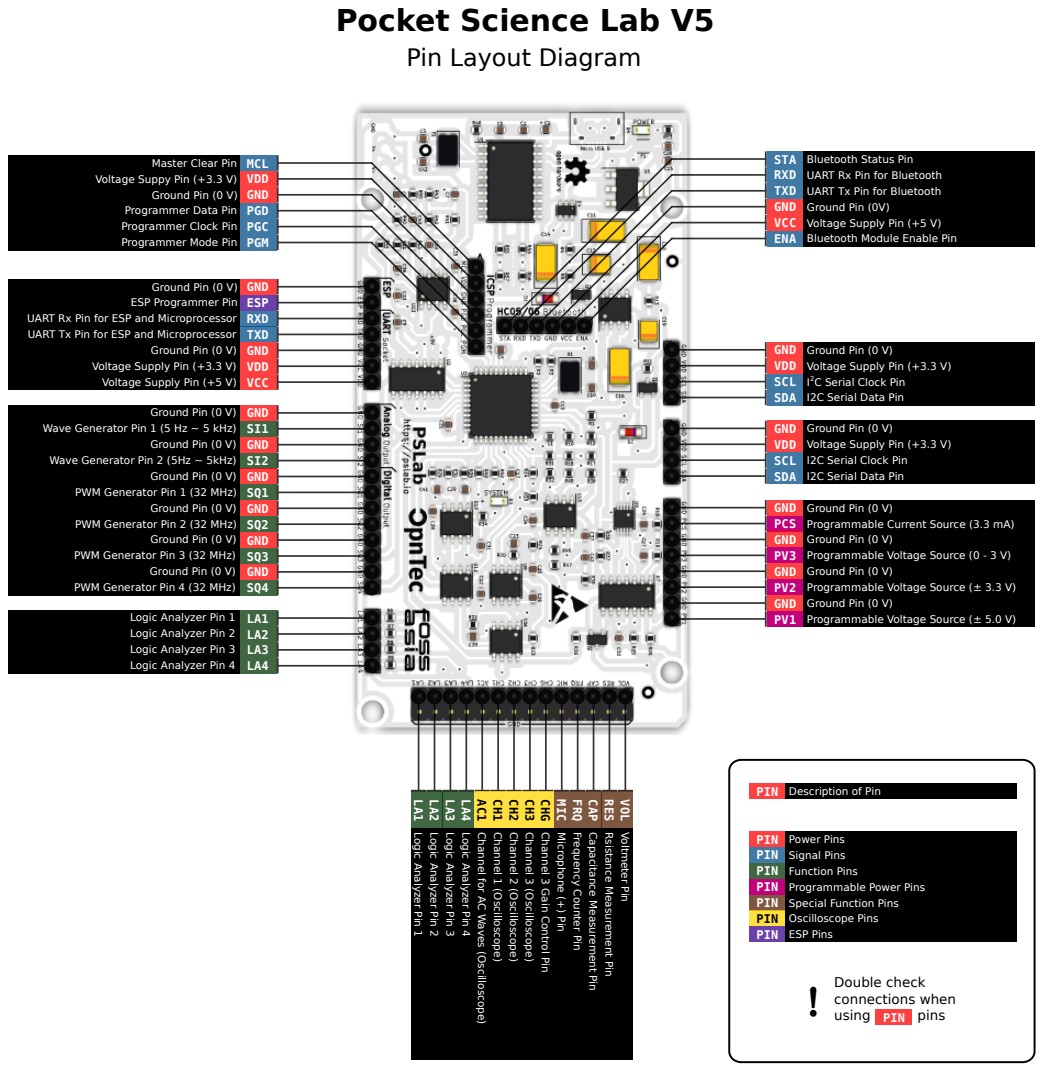
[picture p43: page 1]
2 SCL; C Serial Clock Pin; Channel 1 (Oscilloscope) CH1; Channel 2 (Oscilloscope) CH2; Channel 3 (Oscilloscope) CH3; Master Clear Pin MCL; STA Bluetooth Status Pin; PIN; using; pins

Voltage Suppy Pin (+3.3 V) VDD

RXD UART Rx Pin for Bluetooth
TXD UART Tx Pin for Bluetooth
GND Ground Pin (0V)
VCC Voltage Supply Pin (+5 V)
ENA Bluetooth Module Enable Pin

Ground Pin (0 V) GND
Programmer Data Pin PGD
Programmer Clock Pin PGC
Programmer Mode Pin PGM

ESP Programmer Pin ESP

UART Rx Pin for ESP and Microprocessor RXD
UART Tx Pin for ESP and Microprocessor TXD

GND Ground Pin (0 V)
VDD Voltage Supply Pin (+3.3 V)
SDA I2C Serial Data Pin

Voltage Supply Pin (+3.3 V) VDD
Voltage Supply Pin (+5 V) VCC

Wave Generator Pin 1 (5 Hz ~ 5 kHz) SI1

SCL I2C Serial Clock Pin

Wave Generator Pin 2 (5Hz ~ 5kHz) SI2

PWM Generator Pin 1 (32 MHz) SQ1

PCS Programmable Current Source (3.3 mA)
PV3 Programmable Voltage Source (0 - 3 V)
PV2 Programmable Voltage Source (± 3.3 V)
PV1 Programmable Voltage Source (± 5.0 V)

PWM Generator Pin 2 (32 MHz) SQ2

PWM Generator Pin 3 (32 MHz) SQ3

PWM Generator Pin 4 (32 MHz) SQ4

Logic Analyzer Pin 1 LA1
Logic Analyzer Pin 2 LA2
Logic Analyzer Pin 3 LA3
Logic Analyzer Pin 4 LA4

PIN Description of Pin

Channel for AC Waves (Oscilloscope) AC1

Channel 3 Gain Control Pin CHG

Microphone (+) Pin MIC

Frequency Counter Pin FRQ

Capacitance Measurement Pin CAP

Rsistance Measurement Pin RES

Voltmeter Pin VOL

PIN Power Pins
PIN Signal Pins
PIN Function Pins
PIN Programmable Power Pins
PIN Special Function Pins
PIN Oscilloscope Pins
PIN ESP Pins
Double check
connections when

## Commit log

2022-02-11 refonte 11-02
    [Coûts compression.xlsx, Coûts shredder.xlsx, G14_Gantt_REV.0.xlsx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]
2022-02-11 refonte 11-02 v3
    [engines_data.xlsx]
2022-02-15 mise en place d'une introduction
    [testultime.xlsx]
2022-02-15 CAD transfer
    [580mm 40x40.SLDPRT, Assemblage1.SLDASM, PIED.SLDPRT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]
2022-05-24 Create global view prototype 1 (1).jpg
2022-05-24 Create global view prototype 1 (2).jpg
2022-05-24 Create global view prototype 1 (3).jpg
2022-05-24 Create global view prototype 1 (4).jpg
2022-05-24 Create motor + hopper.jpg
2022-05-24 Create motor coupling (1).jpg
2022-05-24 Create motor coupling (2).jpg
2022-05-24 Create plastic chips size.xlsx
    [plastic chips size.xlsx]
